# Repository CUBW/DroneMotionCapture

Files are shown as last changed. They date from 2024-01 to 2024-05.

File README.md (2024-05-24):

# Table of Contents

1. [System Overview](#1-system-overview)
2. [Basic Build and eCalc Statistics](#2-basic-build-and-ecalc-statistics)
3. [Physical Assembly](#3-physical-assembly)
   - [Flight Controller](#flight-controller)
   - [ESC](#electronic-speed-controller-esc)
   - [Raspberry Pi](#raspberry-pi)
4. [Firmware](#4-firmware)
   - [Flight Controller - ArduPilot/Kakute H7](#flight-controller---ardupilotkakute-h7)
   - [ESC](#electronic-speed-controller-esc-1)
   - [Raspberry Pi](#raspberry-pi-1)
5. [Raspberry Pi Antenna Setup](#5-raspberry-pi-antenna-setup)
   - [Pi ssh setup](#pi-ssh-setup)
   - [Pi UART setup](#pi-uart-setup)
   - [Pi Connection Example](#pi-connection-examples)
   - [Pi button setup](#pi-button-setup)
6. [Calibration/Tuning](#6-calibration/tuning)
   - []

## 1. System Overview
This system was created to create a foundation for more advanced Computer Science and Mechanical Engineering projects.
Goals for this project were:

Presise Control - We have a very small indoor flight space so presicsion/safety was important

Controlled Environment - We wanted the system be simple, but also very accurate, in order for users to be confident there is very little noise or inconsitancey in the system.

Computer Based Control - Lastly wanted control of system to be encapsulated in easy to use code library, allowing begginner proggrammers to use the system without low level knowlegde of communication or flight control. 

Ultimately, with these contraints in mind, we decided to create a Motion Capture Drone system. 
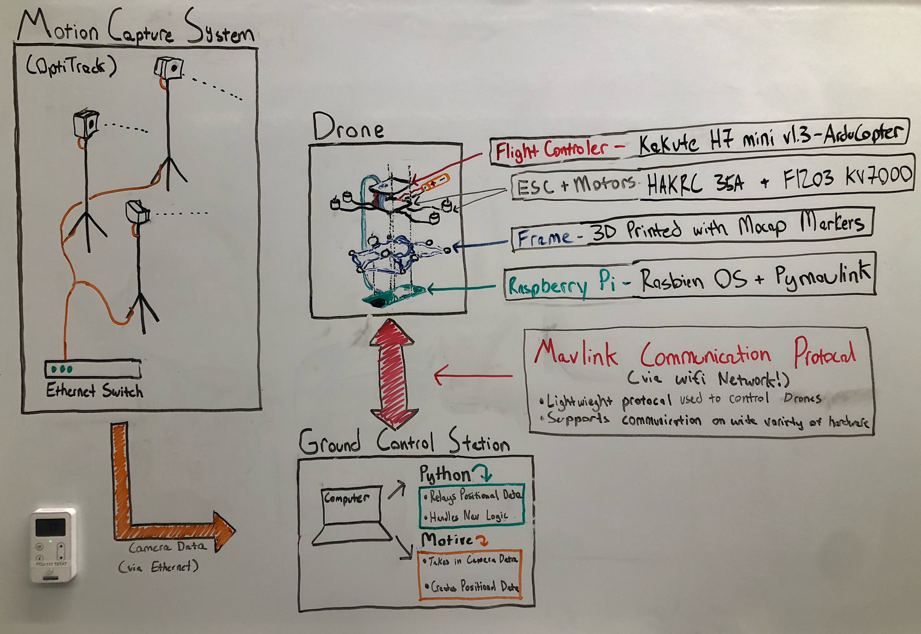
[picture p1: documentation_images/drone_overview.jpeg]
My Image


This system is comprised of three main components:

Drone: Custom built, running ArduCopter firmware, with Raspberry Pi (Using Pymavlink library)

Ground Control Computer: Running Python (Using Pymavlink library) + Motive (Optitrack Software)

Motion Capture System: 6 Cameras connected to ethernet switch (Connected to Ground Control Computer)

This system leverages the existing functionality of ArduCopter Firmware, and Mavlink Communication Protocal. Meaning this system can be immediately be used with ArduCopter UAV's or could be easily adapted to work with any UAV that utilized Mavlink Communication. 

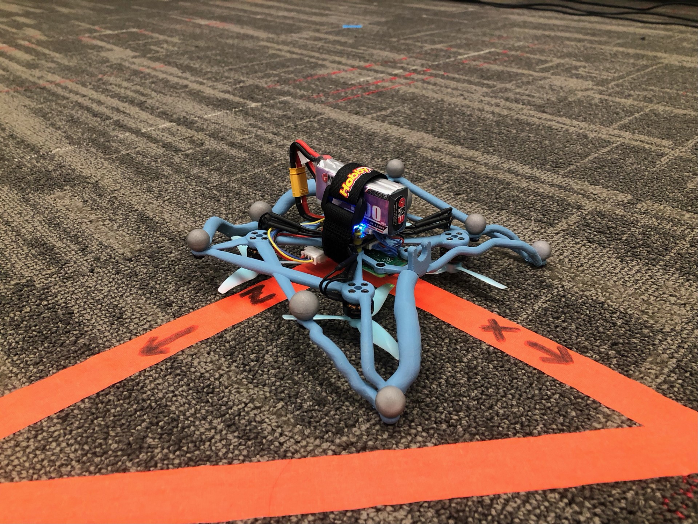
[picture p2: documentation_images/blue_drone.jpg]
My Image

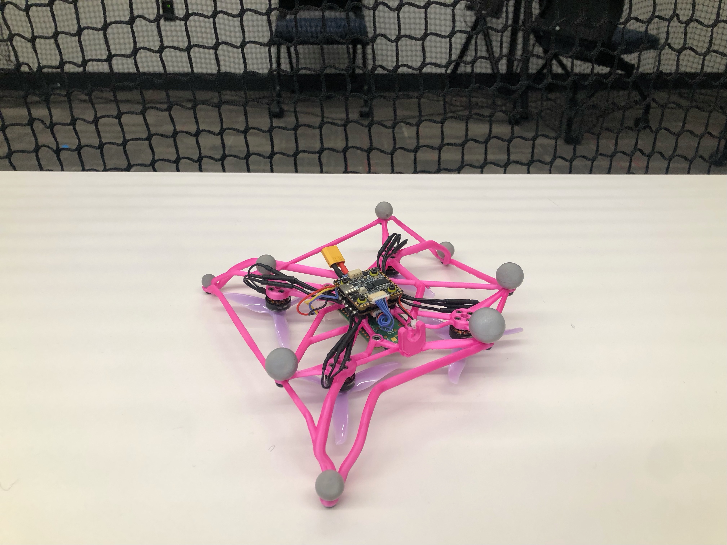
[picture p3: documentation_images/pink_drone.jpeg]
My Image


## 2. Basic Build and eCalc Statistics
First we need to build our drones! To confirm the performance of our proposed custom drone build, we use Ecalc Software. Ecalc takes in information about your custom drone, and predicts metrics such as Thrust:Weight and flight time

Basic Drone parts include, Frame, ESC, Motors, Props, and Batteries. Ecalc will also take into account the power draw of any drone components like Flight controller, FPV camera, and antenna. 
To begin we will make an Excel file with all of proposed parts, with summed weights, and power draws (not including motors)...

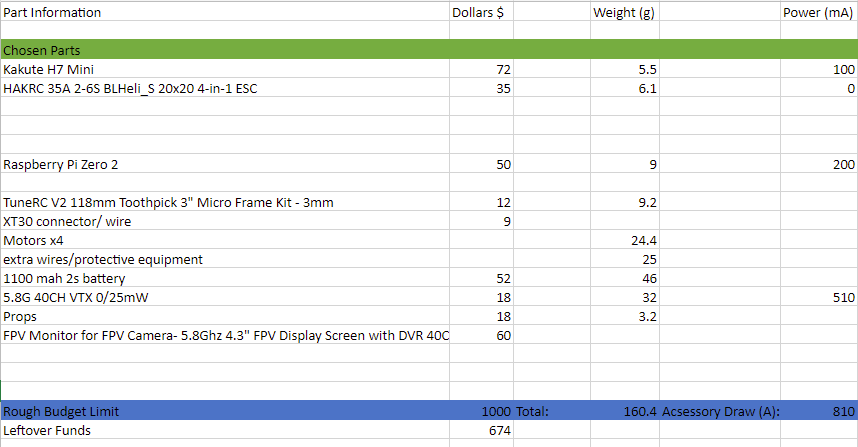
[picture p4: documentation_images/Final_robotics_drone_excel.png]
My Image


Note the totaled weights and power draw. Power draw does NOT include motors. 

Next step is to input this information into Ecalc ... 

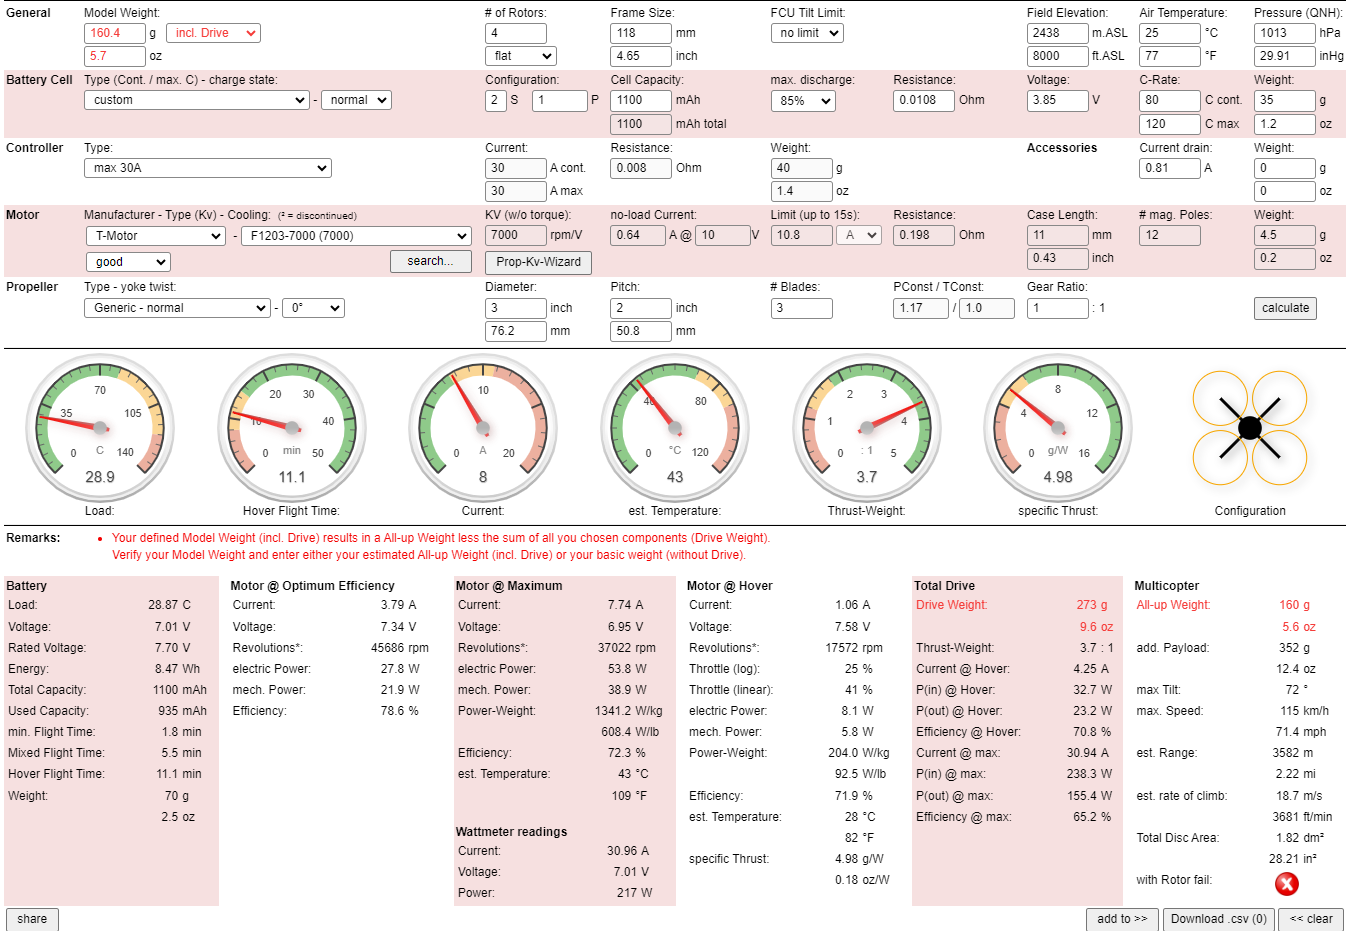
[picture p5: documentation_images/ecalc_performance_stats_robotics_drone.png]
My Image


Note we are using "Including Drive" as our weight option. This is because we have chosen all parts and know the actual weight. The other options beside "include drive" will asume your total weight doesn't include particular components and try to add those weights for you. In this case we can ignore the warning related to total weight, because the estimated weight that ecalc thinks this build should weigh is more than our actual parts. But since we went to the trouble of finding the actual total weight of our drone, we can ignore this. 

Take aways:

In order for our drone to be safely fly, Load, Current, Est. Temp, and Thrust-weight all have to be in the green. If these metrics are in yellow and red, drone my not be able to fly, or prone to damage itself. 

Flight time and Specific Thrust can be in Yellow or Red. Since we are going for an indoor drone with reasonably long flight time, our specific thrust is in the yellow. This is okay because specific thrust relates how effienctly our drone is turning wattage into thrust, and does not relate ablitly to drone to fly or possibly overheat. 

With this ecalc calculation we can confirm our drone will operate correctly with this combination of parts. 

## 3. Physical Assembly
### Flight Controller

For our flight controller we are using  Kakute h7 mini 1.3s. Compatible with Ardupilot Firmware. 

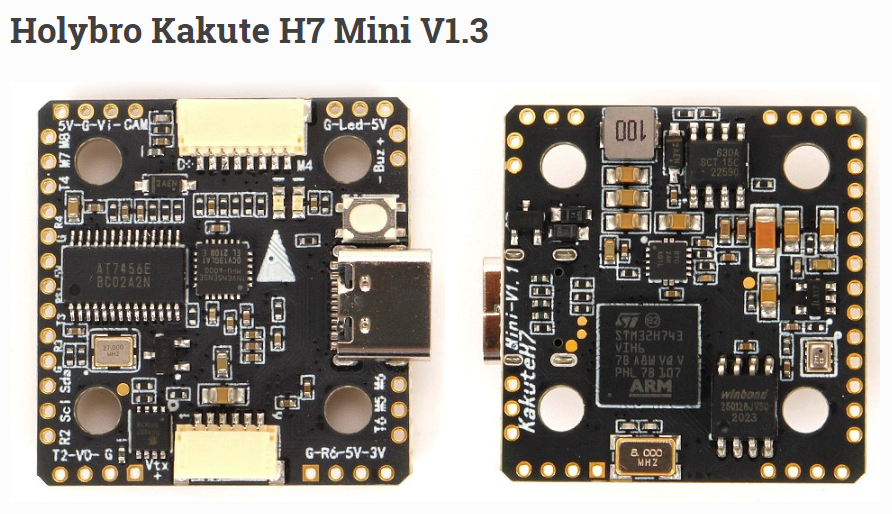
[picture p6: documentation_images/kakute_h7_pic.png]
My Image


For wiring with PI, we are using Pi only as antenna, so we much make four connections, 5v, Ground, Tx (transmit pin), and Rx (recieve pin). 

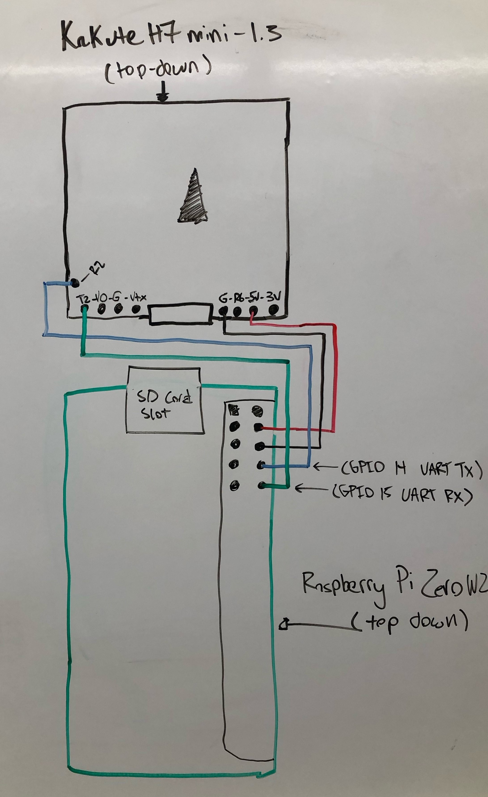
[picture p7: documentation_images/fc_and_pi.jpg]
My Image


For Wiring FPV Camera, our model has it's own antenna, so we only need 5v and GND

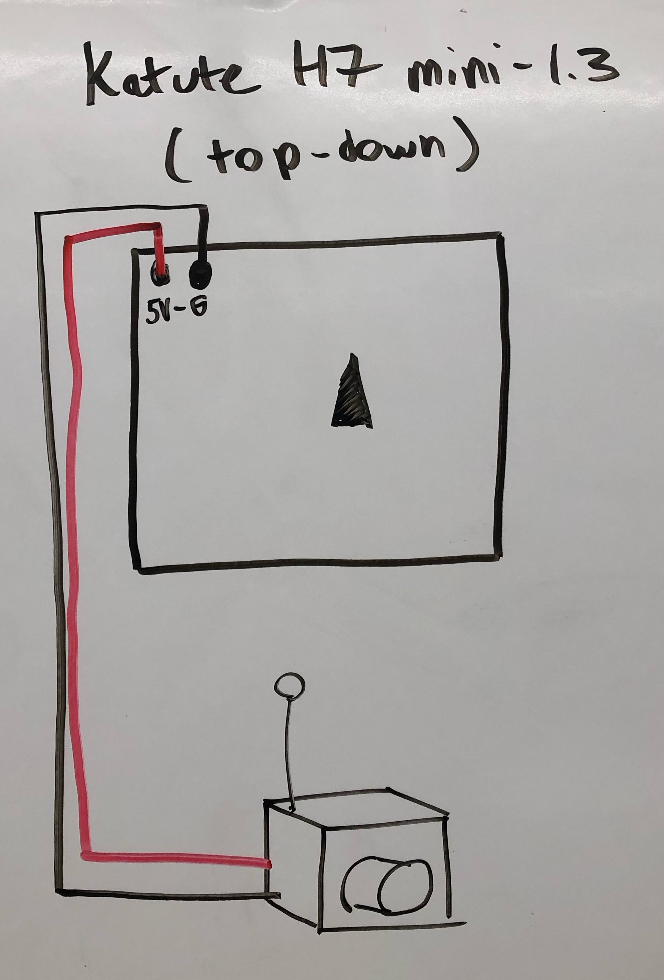
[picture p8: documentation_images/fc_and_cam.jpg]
My Image


### Raspberry Pi
Additionally, we added a button to the raspberry pi in order to properly turn off pi (Pi must be turned off before battery is unplugged, otherwise pi does not shut down correctly). 

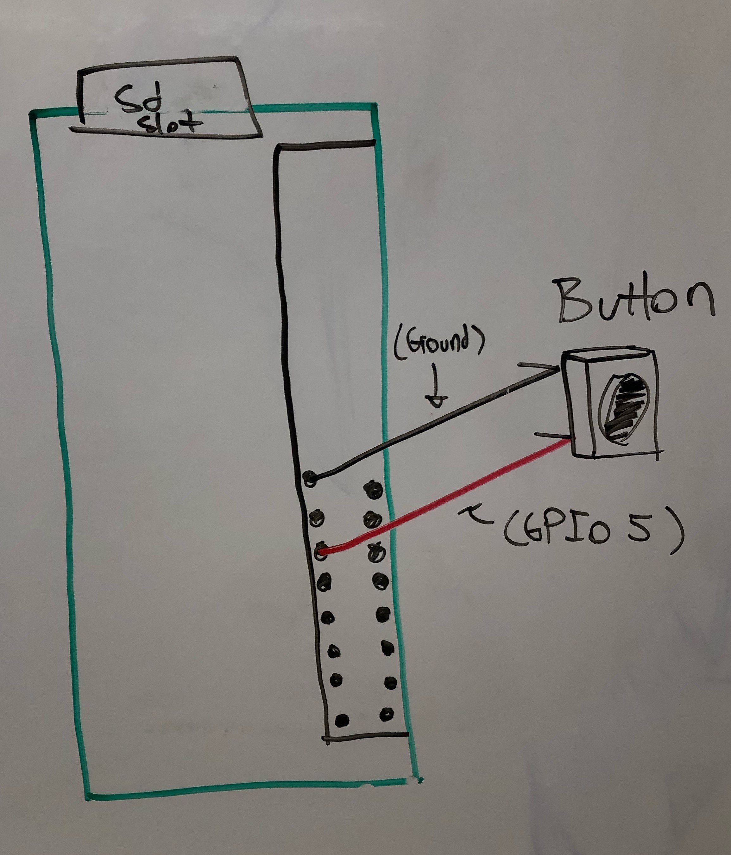
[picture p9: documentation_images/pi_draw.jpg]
My Image


### Electronic Speed Controller (ESC)
Flight controller comes with 6 pin JST connector, but our ESC has a different pin mapping, so the connector has been repinned as such:

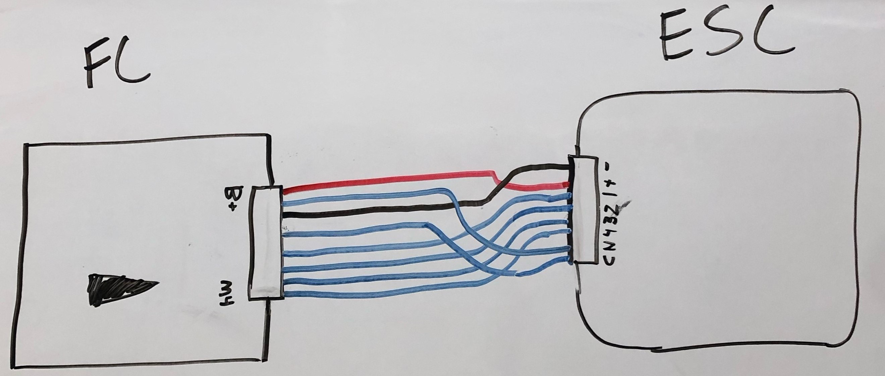
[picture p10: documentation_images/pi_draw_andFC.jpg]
My Image


ESC motor connections in general do not matter, motor will be able to move no matter how the three pins are connected to ESC. The only difference it makes is the direction the motor spins, which you are able to switch in ESC firmware if desired. However for ease of use, we decided to use pin connectors between motor and esc for easy direction swapping...

In addition to motors, a XT30 connector is soldered onto power connections of ESC this connects direclty to 1100mah 2s High Voltage Lipo Battery. 

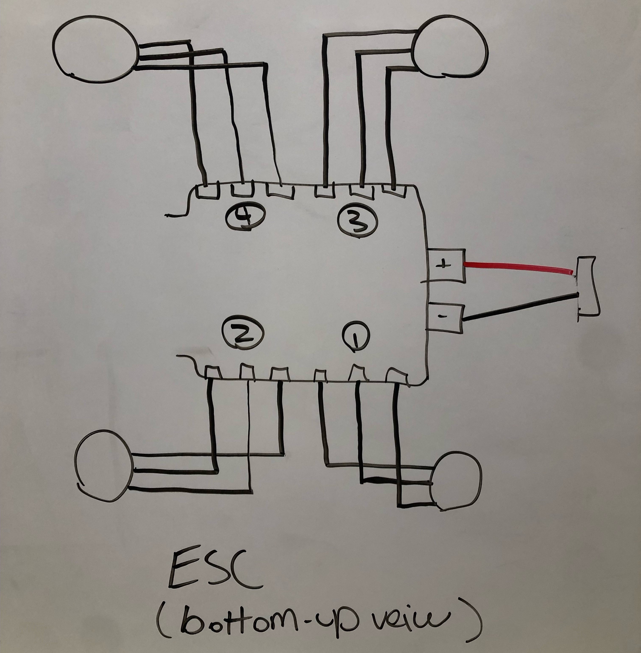
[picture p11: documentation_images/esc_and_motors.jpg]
My Image


## 4. Firmware
### Flight Controller - ArduPilot/Kakute H7
For our flight controller, we decided to use ArduCopter firmware. Exact version is included in Firmware folder. 
Or you can download latest version here: https://firmware.ardupilot.org/Copter/
#### STM32Cube Programmer and ArduCopter ISO
Installation guide follows general ArduCopter installation available here: https://ardupilot.org/copter/docs/common-loading-firmware-onto-chibios-only-boards.html

In Short the steps are: 

1. Download arducopter_with_bl.hex (from repo, or latest from: https://firmware.ardupilot.org/Copter/), we want "with_bl" because your esc is using running BLHeli_s...

2. Download and Install STM32CUBEProgrammer software: https://www.st.com/en/development-tools/stm32cubeprog.html

3. While holding down Kakute H7 mini's DFU button, connect to PC via USB

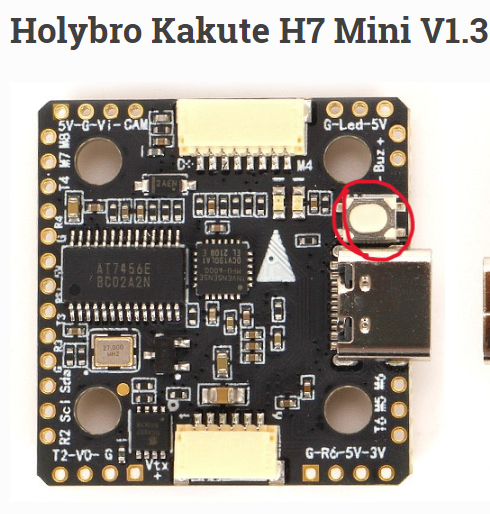
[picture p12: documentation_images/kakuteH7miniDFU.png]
My Image


4. "USB Configuration" hit the refresh button, the port should change from "No DFU detected" to "USB#" # being any number. Hit connect.

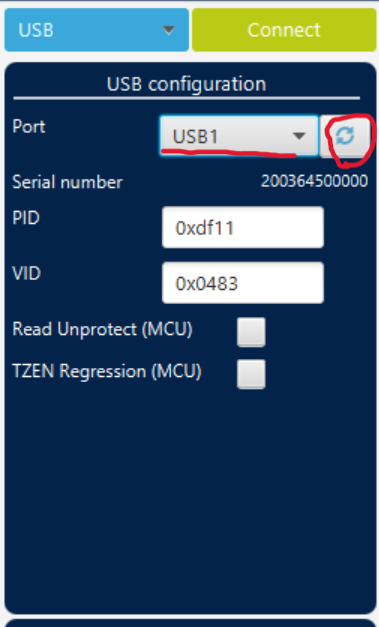
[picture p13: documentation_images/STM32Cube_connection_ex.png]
My Image


Then device information should display at bottom of USB configuration window.

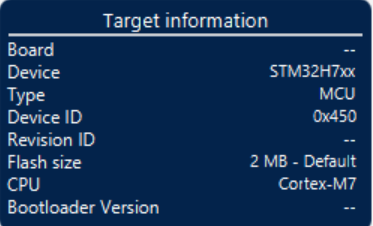
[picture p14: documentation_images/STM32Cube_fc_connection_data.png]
My Image


5. Now click the "open file" tab, and select the previously downloaded "arducopter_with_bl.hex"

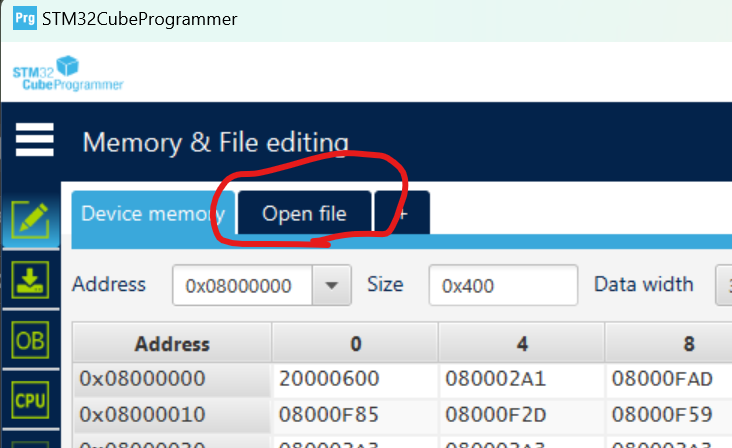
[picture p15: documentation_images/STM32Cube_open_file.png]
My Image


6. Lastly, hit download...

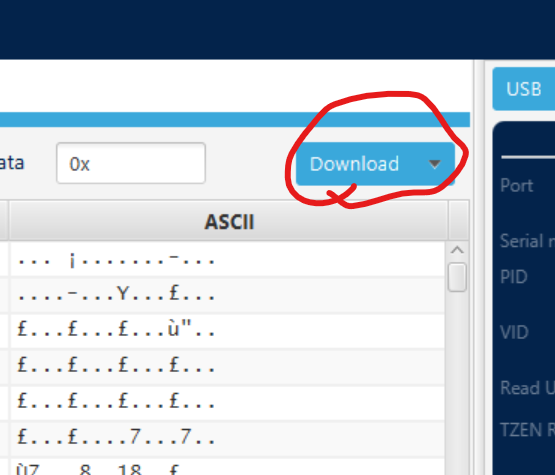
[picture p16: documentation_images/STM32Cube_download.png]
My Image


After this arducopter will install on flight controller and you can disconnect when you are done...

### Electronic Speed Controller (ESC)
Our esc comes with blheli_s, meaning we will use BLHeliSuite to configure esc settings NOT BLheliSuite32. In our setup the only purpose of using BLHeliSuite is to reverse the direction of motors, without rewiring them. You may not need to use this configuration software you don't need to swap directions without rewiring...

#### BLHeliSuite
1. Download and Launch BLHeliSuite, available here: https://www.mediafire.com/folder/dx6kfaasyo24l/BLHeliSuite

2. Power Flight controller and Esc via battery (FC and ESC are connected via the modified 8-pin JST connector referenced in hardware setup for FC). 

3. Once stack is powered by battery, plug flight controller into computer via USB.

4. In BLHeliSuite, click "Select ATMEL/SILABS Interface" drop down, and select "SILABS BLHeli Bootloader (cleanflight)" or the yellow "E". 

My Image

5. Now, in com window, select COM port that FC is currenlty connected under, Hit "connect", then hit "read setup"

My Image

Now you should be connected to ESC settings, and have the ability to modify ESC settings per motor. You can modify a single motor or muiltiple at same time by selecting motor numbers:

My Image

Then you can reversed motor direction for selected motors:

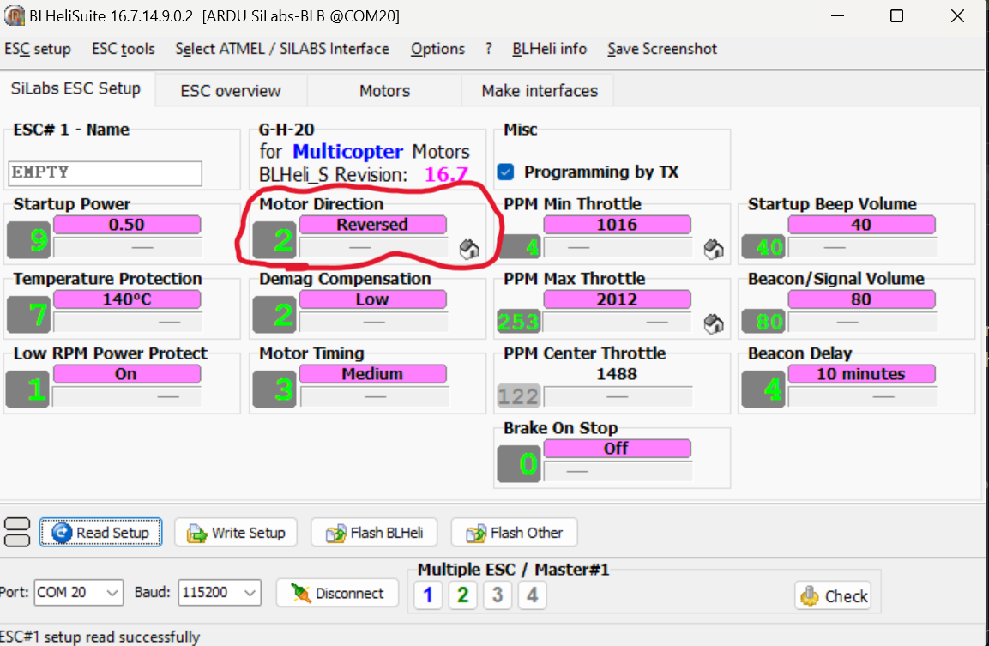
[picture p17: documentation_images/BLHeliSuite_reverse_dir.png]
My Image


### Raspberry Pi
We are using Raspberry Pi Zero 2 W, so we need to flash a Pi OS on an SD card. You can follow official documentation here: https://www.raspberrypi.com/documentation/computers/getting-started.html

Or follow the simplified steps below. 
#### Raspbian Image Flasher

1. Download and Install Rasbien Pi Imager: https://www.raspberrypi.com/software/
2. Start application, and plug in SD Card that Pi OS will be flashed on.
3. Click "Choose Device"

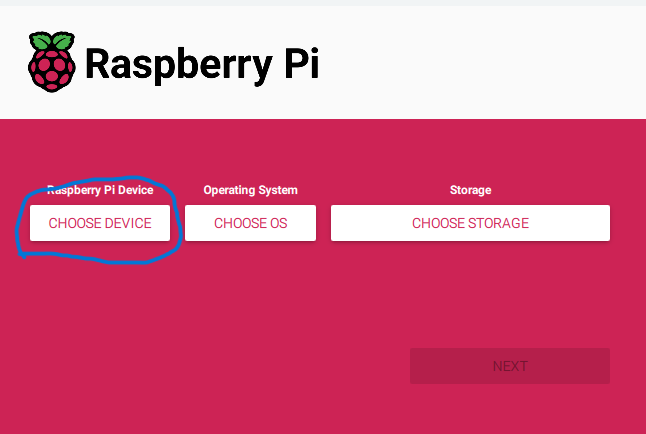
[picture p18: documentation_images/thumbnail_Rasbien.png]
My Image


4. Choose the Pi we are using, in this case Rasberry Pi Zero 2 W

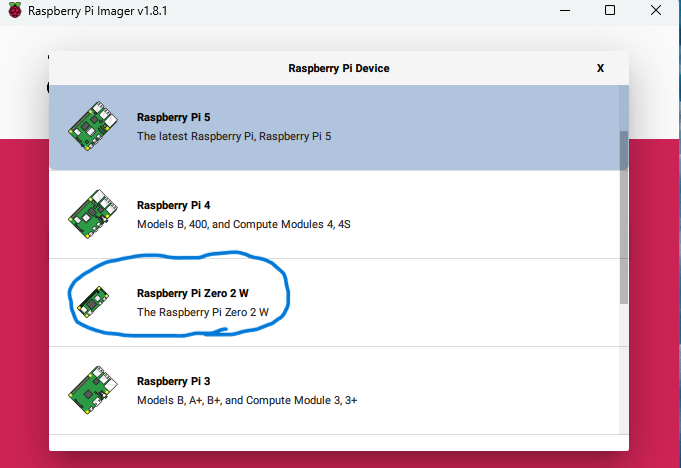
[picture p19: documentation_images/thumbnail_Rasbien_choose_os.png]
My Image

   
5. For the OS, since we have now need for Desktop GUI, we are opting to use "PI OS Lite" (no desktop env). To do this hit "Choose OS"

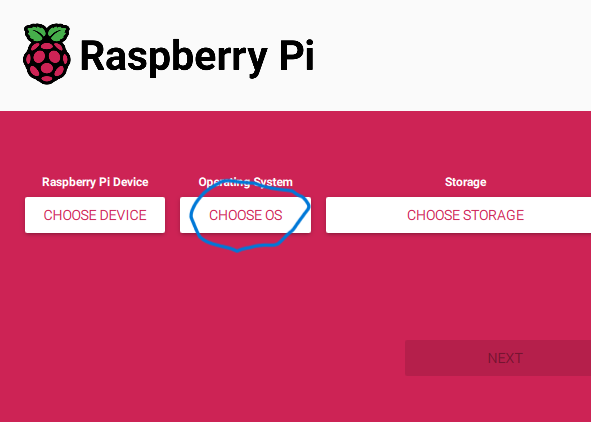
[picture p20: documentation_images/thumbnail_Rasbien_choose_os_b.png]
My Image


6. Select "Other" options

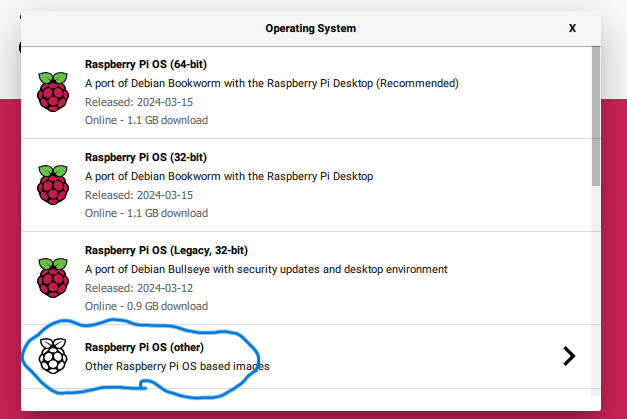
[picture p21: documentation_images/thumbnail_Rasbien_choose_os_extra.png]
My Image


7. Select "PI OS Lite (64 bit) 

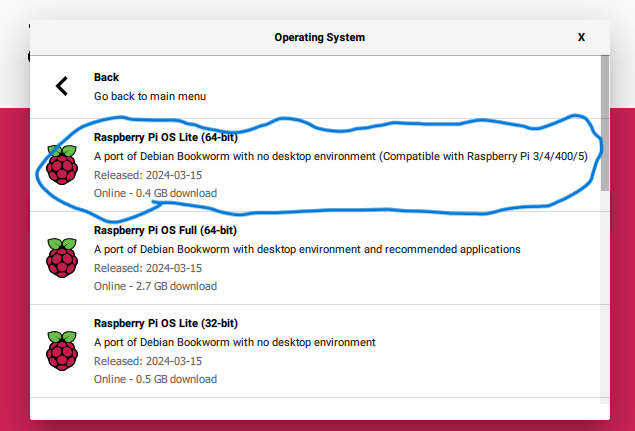
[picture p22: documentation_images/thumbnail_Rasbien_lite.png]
My Image


8. Now we must edit advanced settings, so Pi will automatically connect to a wifi network of our choosing. This is needed because we will be directly SSH into Pi. Select "Next" then seleect "edit settings". OR just click CTR + SHIFT + X on windows and linux. 

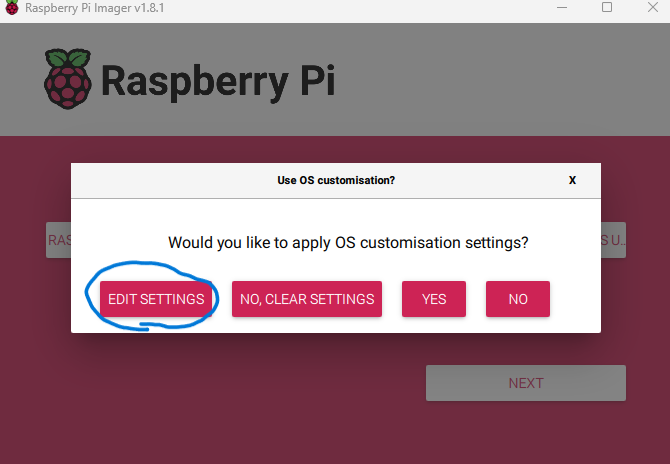
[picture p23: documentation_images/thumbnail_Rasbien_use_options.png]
My Image


9. Fill in all General settings. Hostname, Usernane, and Password will define how pi appears on local network and how to log into it (You will want to remember the username and password you set in "Set Username and Password" section). Configuration of wireless LAN is where you should put your network information (In our case the name and password to our wireless network). 

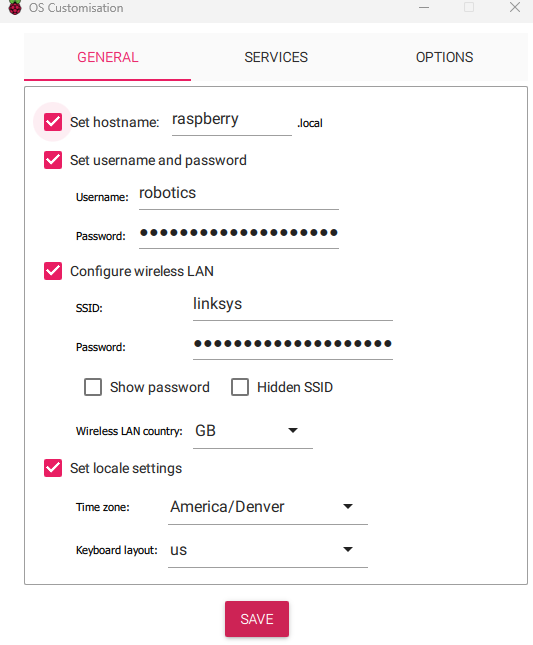
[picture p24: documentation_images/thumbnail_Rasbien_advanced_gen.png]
My Image


10. Next in the "Services" tab, make sure that SSH is enabled.

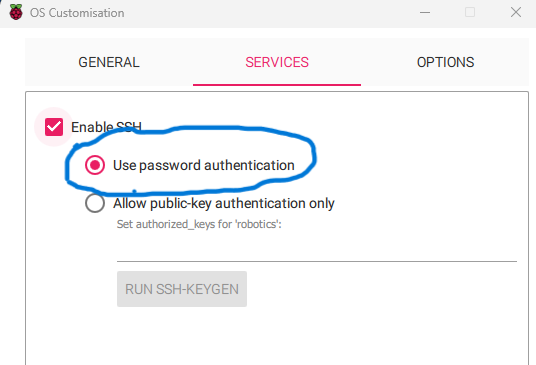
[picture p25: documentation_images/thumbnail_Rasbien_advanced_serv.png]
My Image


11. Lastly save all edited settings, (You don't need to change antything in "Options" Tab). Then confirm flashing of SD Card, then Wait for Rasbien to flash OS. SD Card should be good to plug into Pi once done!

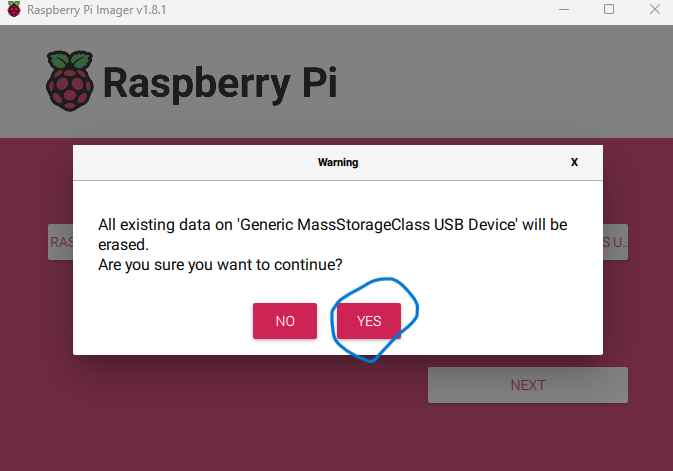
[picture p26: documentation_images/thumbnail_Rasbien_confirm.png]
My Image


## 5. Raspberry Pi Antenna Setup
The setup of Mavlink communication (Drone control) from ground computer through raspberry pi to flight controller follows the basic steps laid out in this guide: https://ardupilot.org/dev/docs/raspberry-pi-via-mavlink.html
Simplified steps for our use case are below...
### Flight Controller Params
First we must change some parameters on our Ardupilot Firmware, if you haven't arealdy installed the ardupilot firmware refer to Flight Controller in "Firmware" Section of documentation. 

We will be ajusting settings using Mission Planner ground control software built for ardupilot, this guide assumes basic knowlege of mission planner, and how to change paremeters. 

If you haven't used mission planner before it's strongly recommned to skim through the documentation, here are some useful links: 

Overview: https://ardupilot.org/dev/docs/raspberry-pi-via-mavlink.html

Installation steps: https://ardupilot.org/planner/docs/mission-planner-installation.html

Basics of Connecting: https://ardupilot.org/planner/docs/common-connect-mission-planner-autopilot.html

1. Connect FC directly to PC via USB C, then connect to FC with Mission Planner.

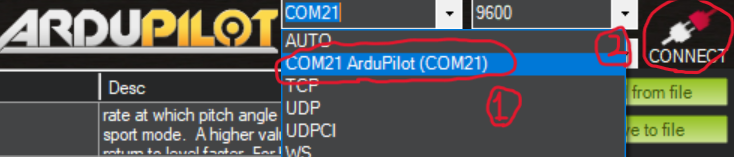
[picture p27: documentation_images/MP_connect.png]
My Image


2. Select "Config" Tab, then "Full Parameter List"

My Image
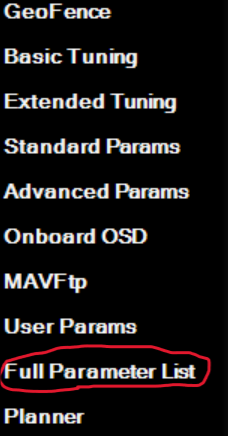
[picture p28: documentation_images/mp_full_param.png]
My Image


3. Change Serial2_protocal to 2 or mavlink 2. "Serial2" in our case are the RX and TX pins on our Kakute H7 mini Flight controller, we are telling the firmware to expect "Mavlink 2" communication protocal on those pins. 

My Image

4. Set Serial2_baud to 57600 (Note offical documentation recommends 921600, in our case we got the system working useing 57600)

My Image

5. Save Params and disconnect.

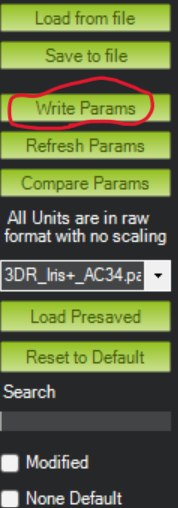
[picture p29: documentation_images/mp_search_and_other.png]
My Image
My Image

Flight contoller is ready to recieve and trasnmit mavlink messages on RX and TX pins that Pi is connectd to.

### Pi ssh setup
To configure Raspberry Pi we opted to SSH into Pi's command line over network. Since during the Pi's OS flasing, we uploaded the settings for Pi to connect automatically to our wifi network. We simply need to find the assigned IP address our local network has given our PI.

1. Power PI (with micro USB). Then, in our local network settings, Locate your routers "Dynamic Host Configuration Protocal Client Table" or "DHCP Cliets List" (This step may vary depending on router and firewall settings on wifi network...) In our case the IP address asigned to our drone is XXX.XXX.X.101, (Note I've put X placeholder in for security, the IP address will be all numbers). Also keep note of our Ground Control Computer in this case "Jayden's Laptop" with IP of XXX.XXX.X.106. 

My Image

2. Open Powershell or equivilant. Type "ssh robotics@XXX.XXX.X.XXX" XXX.XXX.X.XXX being the IP of the Pi we observed earlier. 

My Image

3. If connecting to Pi for first time (Or Ip has been reset for any reason), type "yes" for saving device.

My Image

4. You will then be prompted to type in a password. 
*NOTE: the username (in this case robotics) and password for PI are set when Flashing OS onto SD card, you should have them written down or saved somewhere. Refer to Section "Firmware" subsection "Rasberry PI" step #8 if you are confused...

My Image

If you've done everything correctly you should be SSH'd into PI, and able operate PI via command line interface

My Image

### Pi UART Setup

1. Now that you are ssh'd into pi, we need to open up UART pin to allow for mavlink communication to take place. In rasberry pi cmd line, type "sudo raspi-config"

2. You should open the raspberry pi's configuration menu, from here select "Interfacing Options"

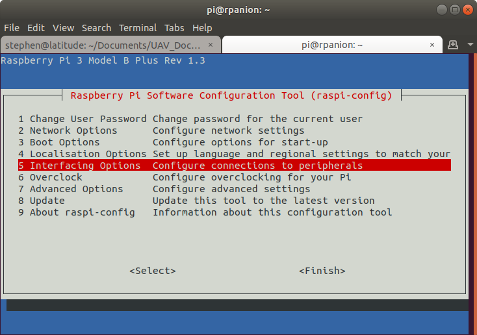
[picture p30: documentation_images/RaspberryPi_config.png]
My Image


3.. Now select "P6 Serial"

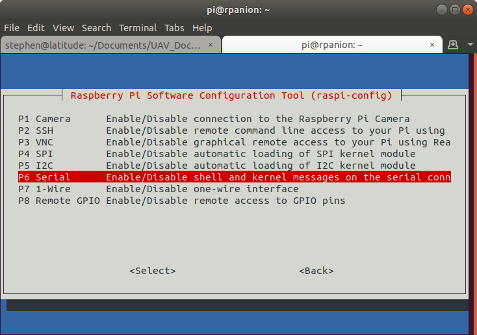
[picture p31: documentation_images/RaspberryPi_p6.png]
My Image


4. When prompted, select no to “Would you like a login shell to be accessible over serial?”.

5. When prompted, select yes to “Would you like the serial port hardware to be enabled?”.

6. Reboot the Raspberry Pi when you are done.

The Raspberry Pi’s serial port will now be usable on /dev/serial0.

### Pi MAVProxy Relay
Now we need to install mavproxy, both on our Pi and our Computer...
the official documentation is here: https://ardupilot.org/mavproxy/docs/getting_started/download_and_installation.html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
Simplified steps are:

1. SSH into Pi
2. Type use this code to install mavproxy (Install all dependencies! It may take 5-10 minutes)
```
sudo apt-get install python3-dev python3-opencv python3-wxgtk4.0 python3-pip python3-matplotlib python3-lxml python3-pygame
pip3 install PyYAML mavproxy --user
echo 'export PATH="$PATH:$HOME/.local/bin"' >> ~/.bashrc
```
For Windows MavProxy install use this installer (visit official documentation if this link is deptricated): https://firmware.ardupilot.org/Tools/MAVProxy/

### Pi Connection Examples
Now that Mavproxy has been installed, we are ready to use Rasberry Pi as "antenna" to control/calibrate our drone!

Example 1, Cmd line control directly from PI SSH Terminal
In this example we will ssh into pi and run MavProxy to connect it to flight controller. And control our drone by typing commands directly into Pi terminal over network

1. Power drone via charged battery (we don't need any wired connections to FC or Pi!)
2. Pi should power on automatically (if everything is wired correctly), SSH into pi
3. Run this code
```
 mavproxy.py --master=/dev/serial0 --baudrate 57600
```

It's important to note with in this example, Mavproxy is only being used as communication between the Pi and FC on the drone. We are using network (ssh) to type commands direclty to PI's terminal (running mavproxy). Ultimately, we want to establish mavlink communication across the network as well, to all allow other programs that use the Mavproxy communication protocal to talk directly to drone over network. see example 2. 

Example 2, Using Mavproxy as "relay" 
In this example we will now run mavproxy, and specify a local IP address for to relay it's mavlink connection to...

1. Access the IP address of your PI and Computer you desire to control drone from. In our case the unique identifiers of our IP addresses are Pi = .101 Computer = .106

My Image

2. SSH into PI, and run this command

Note the master is the same as the first example "/dev/serial0" this is the RX and TX uart connection to FC, the new startup argument out is the destination IP address that you with to relay our communication to. In our case the IP ending in .106

3. Open another PowerShell terminal on your computer, now simpley run mavproxy, no need to specify master or out

Congragulations we've acheived mavproxy communciation over wifi, if mavproxy connected correctly you should see the same cmd line interface for drone control that we saw when were direcly connectd over SSH. The only differnce now is that we have a Mavproxy is being used over network, not just between Pi and FC. 

What does this mean? 

Now that our pi is relaying our mavproxy connection to our computer's IP address. We can now connect with ardupilots "Mission Planner" Ground control software, but instead of using USB C wired connection. We can connect direcly to drone over wifi network. Which means we can now do all our conrol, calibration, and parameter changing wirelessly over the wifi network!

Example 3, connecting to drone with mission planner over network 

1. SSH into pi
2. Run Mavproxy code with XXX.XXX.X.XXX being the IP of your computer
3. Open Mission Planner, and in connection tab select "UDP", Baudrate of "57600" and port number of 14550

Now we are connected wirelessly with Mission planner!

### Pi Button Setup

## Flight Controller Configuration
### Motor, Frame, Propeller, and Battery
### Failsafes and Warnings
### Calibration

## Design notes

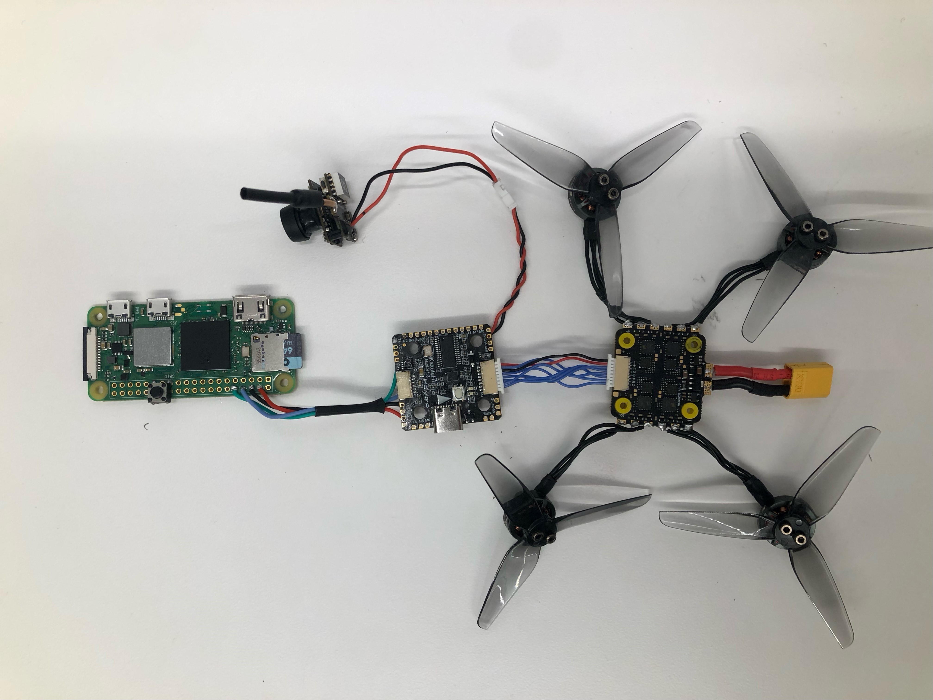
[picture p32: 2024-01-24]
documentation_images/whole_drone_pic.jpg

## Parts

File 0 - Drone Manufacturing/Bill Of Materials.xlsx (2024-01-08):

Part Information | Dollars $ |  | Weight (g) |  | Power (mA) | Shopping URL's | rough Delivery Time (days) | Documentation
Chosen Parts
Kakute H7 Mini | 72 |  | 5.5 |  | 100 | https://holybro.com/products/kakute-h7-mini
HAKRC 35A 2-6S BLHeli_S 20x20 4-in-1 ESC | 35 |  | 6.1 |  | 0 | https://www.getfpv.com/hakrc-35a-2-6s-blheli-s-20x20-4-in-1-esc.html
Raspberry Pi Zero 2 | 50 |  | 9 |  | 200 | https://www.sparkfun.com/products/18713?src=raspberrypi
TuneRC V2 118mm Toothpick 3" Micro Frame Kit - 3mm | 12 |  | 9.2 |  |  | https://www.racedayquads.com/products/tunerc-v2-118mm-3-toothpick-frame-kit-3mm?keyword=frame%203%22
XT30 connector/ wire | 9 |  |  |  |  | https://www.amazon.com/Hobbypark-Connectors-Silicone-Battery-Airplanes/dp/B08J7WPMD9
Motors x4 |  |  | 24.4
extra wires/protective equipment |  |  | 25
1100 mah 2s battery | 52 |  | 46 |  |  | https://www.amazon.com/GAONENG-Battery-1100mAh-Range-Connector/dp/B094NBH89Y
5.8G 40CH VTX 0/25mW | 18 |  | 32 |  | 510 | 5.8 (https://www.amazon.com/AKK-Switchable-600TVL-Camera-Inductrix/dp/B06Y5D8SPZ)
Props | 18 |  | 3.2
FPV Monitor for FPV Camera- 5.8Ghz 4.3" FPV Display Screen with DVR 40CH | 60 |  |  |  |  | https://www.amazon.com/Monitor-Camera-Display-Receiver-800x480/dp/B0BRQB1L2R
Rough Budget Limit | 1000 | Total: | 160.4 | Acsessory Draw (A): | 810
Leftover Funds | 674

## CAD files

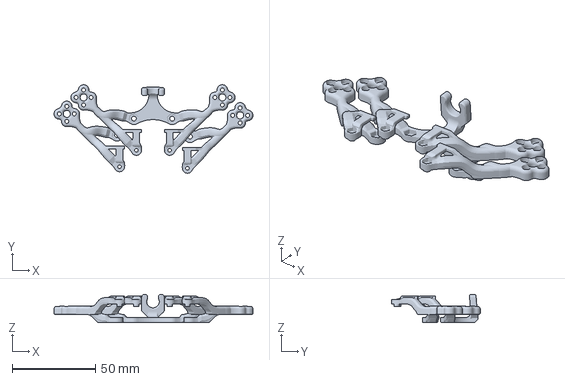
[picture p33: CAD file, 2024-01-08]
0 - Drone Manufacturing/Drone Frame.3mf
119.7 x 53.3 x 17.1 mm

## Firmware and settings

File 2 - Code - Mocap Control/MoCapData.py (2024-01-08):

#Copyright © 2021 Naturalpoint
#
#Licensed under the Apache License, Version 2.0 (the "License")
#you may not use this file except in compliance with the License.
#You may obtain a copy of the License at
#
#http://www.apache.org/licenses/LICENSE-2.0
#
#Unless required by applicable law or agreed to in writing, software
#distributed under the License is distributed on an "AS IS" BASIS,
#WITHOUT WARRANTIES OR CONDITIONS OF ANY KIND, either express or implied.
#See the License for the specific language governing permissions and
#limitations under the License.


# OptiTrack NatNet direct depacketization sample for Python 3.x
#


# Uses the Python NatNetClient.py library to establish a connection (by creating a NatNetClient),
# and receive data via a NatNet connection and decode it using the NatNetClient library.

#Utility functions

import copy
import hashlib
import random

K_SKIP = [0,0,1]
K_FAIL = [0,1,0]
K_PASS = [1,0,0]

# get_tab_str
# generate a string that takes the nesting level into account
def get_tab_str(tab_str, level):
    out_tab_str=""
    loop_range = range(0,level)
    for _ in loop_range:
        out_tab_str+=tab_str
    return out_tab_str

def add_lists(totals, totals_tmp):
    totals[0]+=totals_tmp[0]
    totals[1]+=totals_tmp[1]
    totals[2]+=totals_tmp[2]
    return totals

def test_hash(test_name, test_hash_str, test_object):
    out_str = test_object.get_as_string()
    out_hash_str=hashlib.sha1(out_str.encode()).hexdigest()
    ret_value=True
    if test_hash_str == out_hash_str:
        print("[PASS]:%s"%test_name)
    else:
        print("[FAIL]:%s test_hash_str != out_hash_str"%test_name)
        print("test_hash_str=%s"%test_hash_str)
        print("out_hash_str=%s"%out_hash_str)
        print("out_str =\n%s"%out_str)
        ret_value=False
    return ret_value


def test_hash2(test_name, test_hash_str, test_object, run_test=True):
    ret_value = K_FAIL
    out_str = "FAIL"
    out_str2=""
    indent_string="       "
    if not run_test:
        ret_value = K_SKIP
        out_str = "SKIP"
    elif test_object == None:
        out_str = "FAIL"
        ret_value = K_FAIL
        out_str2 = "%sERROR: test_object was None"%indent_string
    else:

        if str(type(test_object)) != 'NoneType':
            obj_out_str = test_object.get_as_string()
            obj_out_hash_str=hashlib.sha1(obj_out_str.encode()).hexdigest()

        if test_hash_str == obj_out_hash_str:
            out_str = "PASS"
            ret_value = K_PASS
        else:
            out_str2+="%s%s test_hash_str != out_hash_str\n"%(indent_string,test_name)
            out_str2+="%stest_hash_str=%s\n"%(indent_string,test_hash_str)
            out_str2+="%sobj_out_hash_str=%s\n"%(indent_string,obj_out_hash_str)
            out_str2+="%sobj_out_str =\n%s"%(indent_string,obj_out_str)
            ret_value = K_FAIL
    print("[%s]:%s"%(out_str,test_name))

    if len(out_str2):
        print("%s"%out_str2)
    return ret_value


def get_as_string(input_str):
    type_input_str=str(type(input_str))
    if type_input_str == "<class 'str'>":
        return input_str
    elif type_input_str ==  "<class 'NoneType'>":
        return ""
    elif type_input_str == "<class 'bytes'>":
        return input_str.decode('utf-8')
    else:
        print("type_input_str = %s NOT HANDLED"%type_input_str)
        return input_str


#MoCap Frame Classes
class FramePrefixData:
    def __init__(self, frame_number):
        self.frame_number=frame_number

    def get_as_string(self,tab_str="  ", level = 0):
        out_tab_str = get_tab_str(tab_str, level)
        out_str = "%sFrame #: %3.1d\n"%(out_tab_str,self.frame_number)
        return out_str

class MarkerData:
    def __init__(self):
        self.model_name=""
        self.marker_pos_list=[]

    def set_model_name(self, model_name):
        self.model_name = model_name

    def add_pos(self, pos):
        self.marker_pos_list.append(copy.deepcopy(pos))
        return len(self.marker_pos_list)


    def get_num_points(self):
        return len(self.marker_pos_list)


    def get_as_string(self, tab_str="  ", level=0):
        out_tab_str = get_tab_str(tab_str, level)
        out_tab_str2 = get_tab_str(tab_str, level+1)
        out_str=""
        out_str+="%sMarkerData:\n"%out_tab_str
        if self.model_name != "":
            out_str+="%sModel Name : %s\n"%(out_tab_str, get_as_string(self.model_name))
        marker_count = len(self.marker_pos_list)
        out_str+="%sMarker Count :%3.1d\n"%(out_tab_str, marker_count)
        for i in range(marker_count):
            pos = self.marker_pos_list[i]
            out_str+="%sMarker %3.1d pos : [x=%3.2f,y=%3.2f,z=%3.2f]\n"%(out_tab_str2,i,pos[0], pos[1], pos[2])
        return out_str

class MarkerSetData:
    def __init__(self):
        self.marker_data_list=[] #List of Mocap data, the contents of which we will send to the drone
        self.unlabeled_markers=MarkerData()
        self.unlabeled_markers.set_model_name("")

    def add_marker_data(self, marker_data):
        self.marker_data_list.append(copy.deepcopy(marker_data))
        return len(self.marker_data_list)

    def add_unlabeled_marker(self, pos):
        self.unlabeled_markers.add_pos(pos)

    def get_marker_set_count(self):
        return len(self.marker_data_list)

    def get_unlabeled_marker_count(self):
        return self.unlabeled_markers.get_num_points()
    def get_as_string(self, tab_str="  ", level=0):
        out_tab_str  = get_tab_str(tab_str, level)


        out_str=""

        # Labeled markers count
        marker_data_count = len(self.marker_data_list)
        out_str+= "%sMarker Set Count:%3.1d\n"% (out_tab_str,marker_data_count)
        for marker_data in self.marker_data_list:
            out_str += marker_data.get_as_string(tab_str,level+1)

        # Unlabeled markers count (4 bytes)
        unlabeled_markers_count = self.unlabeled_markers.get_num_points()
        out_str += "%sUnlabeled Markers Count:%3.1d\n"%(out_tab_str, unlabeled_markers_count )
        out_str += self.unlabeled_markers.get_as_string(tab_str,level+1)
        return out_str

class LegacyMarkerData:
    def __init__(self):
        self.marker_pos_list=[]

    def add_pos(self, pos):
        self.marker_pos_list.append(copy.deepcopy(pos))
        return len(self.marker_pos_list)

    def get_marker_count(self):
        return len(self.marker_pos_list)

    def get_as_string(self, tab_str="  ", level=0):
        out_tab_str = get_tab_str(tab_str, level)
        out_tab_str2 = get_tab_str(tab_str, level+1)
        out_str=""
        marker_count = len(self.marker_pos_list)
        out_str+="%sLegacy Marker Count :%3.1d\n"%(out_tab_str, marker_count)
        for i in range(marker_count):
            pos = self.marker_pos_list[i]
            # The line below shows how the points lie in the array, this is what we will send to the drone for position, still working on altitude
            out_str+="%sMarker %3.1d pos : [x=%3.2f,y=%3.2f,z=%3.2f]\n"%(out_tab_str2,i,pos[0], pos[1], pos[2])
        return out_str

class RigidBodyMarker:
    def __init__(self):
        self.pos = [0.0,0.0,0.0]
        self.id_num = 0
        self.size = 0
        self.error = 0

    def get_as_string(self, tab_str="  ", level=0):
        out_tab_str = get_tab_str(tab_str, level)
        out_str = ""
        out_str+="RBMarker:\n"
        out_str += "%sPosition: [%3.2f %3.2f %3.2f]\n"%( out_tab_str, self.pos[0], self.pos[1], self.pos[2] )
        out_str += "%sID      : %3.1d\n"%(out_tab_str, self.id_num)
        out_str += "%sSize    : %3.1d\n"%(out_tab_str, self.size)
        return out_str


class RigidBody:
    def __init__(self, new_id, pos, rot):
        self.id_num = new_id
        self.pos=pos
        self.rot=rot
        self.rb_marker_list=[]
        self.tracking_valid = False
        self.error = 0.0

    def add_rigid_body_marker(self, rigid_body_marker):
        self.rb_marker_list.append(copy.deepcopy(rigid_body_marker))
        return len(self.rb_marker_list)


    def get_as_string(self, tab_str=0, level=0):
        out_tab_str = get_tab_str(tab_str, level)
        out_tab_str2 = get_tab_str(tab_str, level+1)

        out_str=""

        # header
        out_str += "%sID            : %3.1d\n"% (out_tab_str, self.id_num)
        # Position and orientation
        out_str += "%sPosition      : [%3.2f, %3.2f, %3.2f]\n"% (out_tab_str, self.pos[0], self.pos[1], self.pos[2] )
        out_str += "%sOrientation   : [%3.2f, %3.2f, %3.2f, %3.2f]\n"% (out_tab_str, self.rot[0], self.rot[1], self.rot[2], self.rot[3] )

        marker_count = len(self.rb_marker_list)
        marker_count_range = range( 0, marker_count )

        # Marker Data
        if marker_count > 0:
            out_str += "%sMarker Count: %3.1d\n"%(out_tab_str, marker_count )
            for i in marker_count_range:
                out_str += "%sMarker %3.1d\n"%(out_tab_str2, i)
                rbmarker = self.rb_marker_list[i]
                out_str += rbmarker.get_as_string(tab_str, level+2)

        out_str += "%sMarker Error  : %3.2f\n"% (out_tab_str, self.error)

        # Valid Tracking
        tf_string = 'False'
        if self.tracking_valid:
            tf_string = 'True'
        out_str += "%sTracking Valid: %s\n"%(out_tab_str, tf_string)

        return out_str


class RigidBodyData:
    def __init__(self):
        self.rigid_body_list=[]


    def add_rigid_body(self, rigid_body):
        self.rigid_body_list.append(copy.deepcopy(rigid_body))
        return len(self.rigid_body_list)


    def get_rigid_body_count(self):
        return len(self.rigid_body_list)


    def get_as_string(self, tab_str="  ", level=0):
        out_tab_str = get_tab_str(tab_str, level)
        out_str=""
        rigid_body_count=len(self.rigid_body_list)
        out_str += "%sRigid Body Count: %3.1d\n"%(out_tab_str, rigid_body_count)
        for rigid_body in self.rigid_body_list:
            out_str += rigid_body.get_as_string(tab_str, level+1)
        return out_str

class Skeleton:
    def __init__(self, new_id=0):
        self.id_num=new_id
        self.rigid_body_list=[]


    def add_rigid_body(self, rigid_body):
        self.rigid_body_list.append(copy.deepcopy(rigid_body))
        return len(self.rigid_body_list)


    def get_as_string(self, tab_str="  ", level=0):
        out_tab_str = get_tab_str(tab_str, level)
        out_tab_str2 = get_tab_str(tab_str, level+1)
        out_str=""
        out_str+="Skeleton:\n"
        out_str+="%sID: %3.1d\n"%(out_tab_str, self.id_num)
        rigid_body_count=len(self.rigid_body_list)
        out_str += "%sRigid Body Count: %3.1d\n"%(out_tab_str, rigid_body_count)
        for rb_num in range(rigid_body_count):
            out_str += "%sRigid Body %3.1d\n"%(out_tab_str2, rb_num)
            out_str += self.rigid_body_list[rb_num].get_as_string(tab_str, level+2)
        return out_str


class SkeletonData:
    def __init__(self):
        self.skeleton_list=[]


    def add_skeleton(self, new_skeleton):
        self.skeleton_list.append(copy.deepcopy(new_skeleton))


    def get_skeleton_count(self):
        return len(self.skeleton_list)


    def get_as_string(self, tab_str = "  ", level=0):
        out_tab_str = get_tab_str(tab_str, level)
        out_tab_str2 = get_tab_str(tab_str, level+1)

        out_str = ""
        skeleton_count = len(self.skeleton_list)
        out_str += "%sSkeleton Count: %3.1d\n"%(out_tab_str, skeleton_count)
        for skeleton_num in range(skeleton_count):
            out_str += "%sSkeleton %3.1d\n"%(out_tab_str2, skeleton_num)
            out_str += self.skeleton_list[skeleton_num].get_as_string(tab_str, level+2)
        return out_str

class AssetMarkerData:
    def __init__(self, marker_id, pos, marker_size=0.0, marker_params=0, residual=0.0):
        self.marker_id=marker_id
        self.pos=pos
        self.marker_size=marker_size
        self.marker_params=marker_params
        self.residual=residual

    def get_as_string(self, tab_str="  ", level=0):
        out_tab_str = get_tab_str(tab_str, level)
        out_tab_str2 = get_tab_str(tab_str, level+1)
        out_str=""
        out_str+="%sID       : %s\n"%(out_tab_str, get_as_string(self.marker_id))
        out_str+="%sPos      : %3.2f %3.2f %3.2f\n"%(out_tab_str, self.pos[0], self.pos[1], self.pos[2])
        out_str+="%sSize     : %3.2f\n"%(out_tab_str, self.marker_size)
        out_str+="%sParams   : %s\n"%(out_tab_str, self.marker_params)
        out_str+="%sResidual : %3.2f\n"%(out_tab_str, self.residual)

        return out_str

class AssetRigidBodyData:
    def __init__(self, new_id, pos, rot, mean_error=0.0, param=0):
        self.id_num=new_id
        self.pos = pos
        self.rot = rot
        self.mean_error = mean_error
        self.param = param

    def get_as_string(self, tab_str="  ", level=0):
        out_tab_str = get_tab_str(tab_str, level)
        out_str=""
        out_str += "%sID          : %s\n"%(out_tab_str, get_as_string(self.marker_id))
        out_str += "%sPosition    : %3.2f %3.2f %3.2f\n"%(out_tab_str, self.pos[0], self.pos[1], self.pos[2])
        out_str += "%sOrientation : %3.2f %3.2f %3.2f %3.2f\n"%(out_tab_str, self.rot[0], self.rot[1], self.rot[2], self.rot[3])
        out_str += "%sMean Error  : %3.2f\n"%(out_tab_str, self.mean_error)
        out_str += "%sParam       : %s\n"%(out_tab_str, self.param)

        return out_str

class AssetData:
    def __init__(self):
        self.asset_id=0
        self.asset_rigid_body_list=[]
        self.asset_marker_list=[]

    def set_id(self, new_id):
        self.asset_id=new_id

    def add_rigid_body(self, rigid_body):
        self.rigid_body_list.append(copy.deepcopy(rigid_body))
        return len(self.rigid_body_list)

    def add_marker(self, marker):
        self.marker_list.append(copy.deepcopy(marker))
        return len(self.marker_list)

    def get_rigid_body_count(self):
        return len(self.asset_rigid_body_list)

    def get_marker_count(self):
        return len(self.asset_marker_list)

    def get_as_string(self, tab_str = "  ", level = 0):
        out_tab_str = get_tab_str(tab_str, level)

        out_str = ""
        out_str+="%sAssetData:\n"%out_tab_str
        out_str += "%sID          :%s"%(out_tab_str,get_as_string(self.asset_id))
        rigid_body_count = len(self.rigid_body_list)
        out_str += "%srigid_body Count: %3.1d\n"%(out_tab_str, rigid_body_count)
        for i in range(rigid_body_count):
            out_str += self.rigid_body_list[i].get_as_string(tab_str, level+1, i)

        marker_count = len(self.marker_list)
        out_str += "%smarker Count: %3.1d\n"%(out_tab_str, marker_count)
        for i in range(marker_count):
            out_str += self.marker_list[i].get_as_string(tab_str, level+1, i)

        return out_str


class LabeledMarker:
    def __init__(self, new_id, pos, size=0.0, param = 0, residual=0.0):
        self.id_num=new_id
        self.pos = pos
        self.size = size
        self.param = param
        self.residual = residual
        if str(type(size)) == "<class 'tuple'>":
            self.size=size[0]

    def __decode_marker_id(self):
        model_id = self.id_num >> 16
        marker_id = self.id_num & 0x0000ffff
        return model_id, marker_id

    def __decode_param(self):
        occluded = ( self.param & 0x01 ) != 0
        point_cloud_solved = ( self.param & 0x02 ) != 0
        model_solved = ( self.param & 0x04 ) != 0
        return occluded,point_cloud_solved, model_solved

    def get_as_string(self, tab_str, level):
        out_tab_str = get_tab_str(tab_str, level)
        model_id, marker_id = self.__decode_marker_id()
        out_str = ""
        out_str+="%sLabeledMarker:\n"%out_tab_str
        out_str += "%sID                 : [MarkerID: %3.1d] [ModelID: %3.1d]\n"%(out_tab_str, marker_id,model_id)
        out_str += "%spos                : [%3.2f, %3.2f, %3.2f]\n"%(out_tab_str, self.pos[0],self.pos[1],self.pos[2])
        out_str += "%ssize               : [%3.2f]\n"%(out_tab_str, self.size)

        occluded, point_cloud_solved, model_solved = self.__decode_param()
        out_str += "%soccluded           : [%3.1d]\n"%(out_tab_str, occluded)
        out_str += "%spoint_cloud_solved : [%3.1d]\n"%(out_tab_str, point_cloud_solved)
        out_str += "%smodel_solved       : [%3.1d]\n"%(out_tab_str, model_solved)
        out_str += "%serr                : [%3.2f]\n"%(out_tab_str, self.residual)

        return out_str


class LabeledMarkerData:
    def __init__(self):
        self.labeled_marker_list=[]

    def add_labeled_marker(self, labeled_marker):
        self.labeled_marker_list.append(copy.deepcopy(labeled_marker))
        return len(self.labeled_marker_list)

    def get_labeled_marker_count(self):
        return len(self.labeled_marker_list)

    def get_as_string(self, tab_str = "  ", level = 0):
        out_tab_str = get_tab_str(tab_str, level)
        out_tab_str2 = get_tab_str(tab_str, level+1)
        out_str = ""

        labeled_marker_count = len(self.labeled_marker_list)
        out_str += "%sLabeled Marker Count:%3.1d\n"%(out_tab_str, labeled_marker_count )
        for i in range( 0, labeled_marker_count ):
            out_str += "%sLabeled Marker %3.1d\n"%(out_tab_str2,i)
            labeled_marker = self.labeled_marker_list[i]
            out_str += labeled_marker.get_as_string(tab_str, level+2)
        return out_str

class ForcePlateChannelData:
    def __init__(self):
        # list of floats
        self.frame_list=[]


    def add_frame_entry(self, frame_entry):
        self.frame_list.append(copy.deepcopy(frame_entry))
        return len(self.frame_list)


    def get_as_string(self, tab_str, level, channel_num = -1):
        fc_max = 4
        out_tab_str  = get_tab_str(tab_str, level)

        out_str = ""
        frame_count = len(self.frame_list)
        fc_show = min(frame_count, fc_max)
        out_str += "%s"%(out_tab_str)
        if channel_num >= 0 :
            out_str += "Channel %3.1d: "%channel_num
        out_str += "%3.1d Frames - Frame Data: "%(frame_count)
        for i in range(fc_show):
            out_str += "%3.2f "%(self.frame_list[i])
        if fc_show < frame_count :
            out_str += " - Showing %3.1d of %3.1d frames"%(fc_show, frame_count)
        out_str += "\n"
        return out_str

class ForcePlate:
    def __init__(self, new_id=0):
        self.id_num = new_id
        self.channel_data_list=[]

    def add_channel_data(self, channel_data):
        self.channel_data_list.append(copy.deepcopy(channel_data))
        return len(self.channel_data_list)

    def get_as_string(self, tab_str, level):
        out_tab_str = get_tab_str(tab_str, level)
        out_str = ""

        out_str += "%sID           : %3.1d"%(out_tab_str, self.id_num)
        num_channels = len(self.channel_data_list)
        out_str += "%sChannel Count: %3.1d\n"%(out_tab_str, num_channels)
        for i in range(num_channels):
            out_str += self.channel_data_list[i].get_as_string(tab_str, level+1,i)
        return out_str

class ForcePlateData:
    def __init__(self):
        self.force_plate_list=[]

    def add_force_plate(self, force_plate):
        self.force_plate_list.append(copy.deepcopy(force_plate))
        return len(self.force_plate_list)


    def get_force_plate_count(self):
        return len(self.force_plate_list)


    def get_as_string(self, tab_str="  ", level=0):
        out_tab_str = get_tab_str(tab_str, level)
        out_tab_str2 = get_tab_str(tab_str, level+1)
        out_str=""

        force_plate_count = len(self.force_plate_list)
        out_str += "%sForce Plate Count: %3.1d\n"%(out_tab_str, force_plate_count)
        for i in range(force_plate_count):
            out_str += "%sForce Plate %3.1d\n"%(out_tab_str2, i)
            out_str += self.force_plate_list[i].get_as_string(tab_str, level+2)

        return out_str

class DeviceChannelData:
    def __init__(self):
        # list of floats
        self.frame_list=[]


    def add_frame_entry(self, frame_entry):
        self.frame_list.append(copy.deepcopy(frame_entry))
        return len(self.frame_list)


    def get_as_string(self, tab_str, level, channel_num = -1):
        fc_max = 4
        out_tab_str  = get_tab_str(tab_str, level)

        out_str = ""
        frame_count = len(self.frame_list)
        fc_show = min(frame_count, fc_max)
        out_str += "%s"%(out_tab_str)
        if channel_num >= 0:
            out_str += "Channel %3.1d: "%channel_num
        out_str += "%3.1d Frames - Frame Data: "%(frame_count)
        for i in range(fc_show):
            out_str += "%3.2f "%(self.frame_list[i])
        if fc_show < frame_count:
            out_str += " - Showing %3.1d of %3.1d frames"%(fc_show, frame_count)
        out_str += "\n"
        return out_str


class Device:
    def __init__(self, new_id):
        self.id_num=new_id
        self.channel_data_list = []

    def add_channel_data(self, channel_data):
        self.channel_data_list.append(copy.deepcopy(channel_data))
        return len(self.channel_data_list)

    def get_as_string(self, tab_str, level, device_num):
        out_tab_str = get_tab_str(tab_str, level)

        out_str = ""

        num_channels = len(self.channel_data_list)
        out_str+= "%sDevice %3.1d      ID: %3.1d Num Channels: %3.1d\n"% (out_tab_str, device_num, self.id_num, num_channels )
        for i in range(num_channels):
            out_str += self.channel_data_list[i].get_as_string(tab_str, level+1, i)

        return out_str
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

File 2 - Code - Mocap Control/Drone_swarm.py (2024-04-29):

import sys
import time
from Custom_Drone_Commands import *
from Custom_Mocap_Commands import *   


###### MAIN ######
init_time = time.time()

num_of_drones = 2

# Mocap connection:
streaming_client = mocap_connect()

is_running = streaming_client.run()


# Drone connection
swarm_ports = [14550, 14551, 14552] 
swarm_connections= []
swarm_mocap_streaming_threads = []

for port in swarm_ports:
    connection = drone_connect(port)
    swarm_connections.append(connection)

time.sleep(3)
# Mocap Streaming Thread, will run until you terminate THIS's files terminal.

swarm_rigid_body_id_list = [6,9,8]

stream_id = 1
for id, connection in zip(swarm_rigid_body_id_list, swarm_connections):
    stream_id_string = "stream" + str(stream_id)
    threaded_mocap_drone_stream = threaded_mocap_streaming(stream_id_string, stream_id, connection, streaming_client, init_time, id)
    swarm_mocap_streaming_threads.append(threaded_mocap_drone_stream)

accuracy = .10

for drone_mocap_thread_stream in swarm_mocap_streaming_threads:
    drone_mocap_thread_stream.start()

time.sleep(2)
for drone_connection in swarm_connections:
    set_drone_gps_global_origin(drone_connection)
time.sleep(3)

take_off_height = .5
drone1_takeoff_thread = TakeoffThread(swarm_connections[0], take_off_height, accuracy, init_time)
drone2_takeoff_thread = TakeoffThread(swarm_connections[1], take_off_height, accuracy, init_time)
drone3_takeoff_thread = TakeoffThread(swarm_connections[2], take_off_height, accuracy, init_time)

drone1_takeoff_thread.start()
drone2_takeoff_thread.start()
drone3_takeoff_thread.start()

drone1_takeoff_thread.join()
drone2_takeoff_thread.join()
drone3_takeoff_thread.join()

time.sleep(1)

print("all drones have taken off")


accuracy = .15

# swarm_target_positions = [[-1,.5,-.5],[0,.5,-.5],[1,.5,-.5]]
# goto_ned_threads = []

# for drone_connection, target_position in zip(swarm_connections, swarm_target_positions):
#     x = target_position[0]
#     y = target_position[1]
#     z = target_position[2]
#     goto_NED_point_thread = GotoNEDPointThread(drone_connection, x, y, z, init_time, accuracy)
#     goto_ned_threads.append(goto_NED_point_thread)

# for thread in goto_ned_threads:
#     thread.start()

# for thread in goto_ned_threads:
#     thread.join()

# swarm_target_positions = [[-1,-.5,-.5],[0,0,-.5],[1,-.5,-.5]]
# goto_ned_threads = []

# for drone_connection, target_position in zip(swarm_connections, swarm_target_positions):
#     x = target_position[0]
#     y = target_position[1]
#     z = target_position[2]
#     goto_NED_point_thread = GotoNEDPointThread(drone_connection, x, y, z, init_time, accuracy)
#     goto_ned_threads.append(goto_NED_point_thread)

# for thread in goto_ned_threads:
#     thread.start()

# for thread in goto_ned_threads:
#     thread.join()


# swarm_target_positions = [[-1,0,-.5],[0,0,-.5],[1,0,-.5]]
# goto_ned_threads = []

# for drone_connection, target_position in zip(swarm_connections, swarm_target_positions):
#     x = target_position[0]
#     y = target_position[1]
#     z = target_position[2]
#     goto_NED_point_thread = GotoNEDPointThread(drone_connection, x, y, z, init_time, accuracy)
#     goto_ned_threads.append(goto_NED_point_thread)

# for thread in goto_ned_threads:
#     thread.start()

# for thread in goto_ned_threads:
#     thread.join()

rotating_triangle = RotatingTriangle(25)

iterations = 20

accuracy = .20

while True:
    swarm_target_positions = rotating_triangle.get_triangle_coordinates()

    goto_ned_threads = []

    for drone_connection, target_position in zip(swarm_connections, swarm_target_positions):
        x = target_position[0]
        y = target_position[1]
        z = target_position[2]
        goto_NED_point_thread = GotoNEDPointThread(drone_connection, x, y, z, init_time, accuracy)
        goto_ned_threads.append(goto_NED_point_thread)

    for thread in goto_ned_threads:
        thread.start()

    for thread in goto_ned_threads:
        thread.join()
    iterations = iterations -1

    if iterations == 0:
        break


for drone in swarm_connections:
    set_mode_land(drone)

for drone in swarm_connections:
    disarm(drone)


time.sleep(2)

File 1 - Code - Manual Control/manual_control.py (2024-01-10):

from pickletools import float8
from pymavlink import mavutil
import math
import tkinter as tk
import pygame
import transformations as tft
from pyquaternion import Quaternion
import time

def get_distance_global(current_lat, current_lon, target_lat, target_lon):
    #return the distance between current position and target position in centimeters
    #does not account for the curvature of the earth

    delta_lat = target_lat - current_lat
    delta_lon = target_lon - current_lon

    if delta_lat <= 1 or delta_lon <= 1:
        return 0

    distance  = math.sqrt(delta_lat ** 2 + delta_lon ** 2) #formula for euclidean distance between 2 points
    return distance #mavlink GPS coords are represented in units of 10,000,000, so this line converts degrees to cm. 

def get_distance_local(curr_x, curr_y, curr_z, x, y, z):
    return math.sqrt((curr_x - x)**2 + (curr_y - y)**2 + (curr_z - z)**2)

def connect(port):
    print("Attempting to connect on port %d" % port)

    connection = mavutil.mavlink_connection('udpin:0.0.0.0:%d' % port) 

    connection.wait_heartbeat() #wait until we hear a heartbeat from the copter

    print("Connection success")
    print("Heartbeat from system (system %u component %u)" % (connection.target_system, connection.target_component))

    return connection 

def takeoff(connection, takeoff_alt):
    #set copter to guided mode
    connection.mav.set_mode_send(connection.target_system, mavutil.mavlink.MAV_MODE_FLAG_CUSTOM_MODE_ENABLED, 4) 

    #arm throttle
    connection.mav.command_long_send(connection.target_system, connection.target_component, 
                                 mavutil.mavlink.MAV_CMD_COMPONENT_ARM_DISARM, 0, 1, 0, 0, 0, 0, 0, 0)

    msg = connection.recv_match(type = 'COMMAND_ACK', blocking = True)
    print(msg) #"result: 0" if it executed without error. If you get result: 4, you probably need to set the copter to guided mode.

    #send takeoff command to target altitude.
    connection.mav.command_long_send(connection.target_system, connection.target_component, 
                                 mavutil.mavlink.MAV_CMD_NAV_TAKEOFF, 0, 0, 0, 0, 0, 0, 0, takeoff_alt)

    msg = connection.recv_match(type = 'COMMAND_ACK', blocking = True)
    print(msg)

    #loop until copter reaches takeoff altitude
    while 1:
        # Wait for the next LOCAL_POSITION_NED message
        msg = connection.recv_match(type='LOCAL_POSITION_NED', blocking=True)
    
        # Check if altitude is within a threshold of the target altitude
        if abs(msg.z * -1 - takeoff_alt) < 1.0:
            print("Reached target altitude")
            break

def land(connection): 
    connection.mav.command_long_send(connection.target_system, connection.target_component, 
                                mavutil.mavlink.MAV_CMD_NAV_LAND, 0, 0, 0, 0, 0, 0, 0, 0)

#send local frame coordinates and have copter fly over that spot.
def send_waypoint_local(connection, x, y, alt):
    connection.mav.send(mavutil.mavlink.MAVLink_set_position_target_local_ned_message
                    (10, connection.target_system, connection.target_component, mavutil.mavlink.MAV_FRAME_LOCAL_NED, 
                     int(0b010111111000), x, y, alt,
                      0, 0, 0, 0, 0, 0, 0, 0))

    while 1:
        msg = connection.recv_match(type = 'LOCAL_POSITION_NED', blocking = True)
        
        current_x = msg.x
        current_y = msg.y
        current_z = msg.z

        print("current x: %d" % current_x)

        distance = get_distance_local(current_x, current_y, current_z, x, y, alt)

        print("distance to target: %d" % distance)

        if(distance <= 3): #break when we are within 50 cm of target
            print("target waypoint reached")
            break


#send global gps coordinates and altitude, and have copter fly over that spot. 
def send_waypoint_global(connection, lat, lon, alt):
    connection.mav.send(mavutil.mavlink.MAVLink_set_position_target_global_int_message
                    (10, connection.target_system, connection.target_component, mavutil.mavlink.MAV_FRAME_GLOBAL_RELATIVE_ALT, 
                     int(0b110111111000), int(lat), int(lon), alt, 0, 0, 0, 0, 0, 0, 0, 0))
    #loop until we reach target waypoint
    while 1:
        msg = connection.recv_match(type = 'GLOBAL_POSITION_INT', blocking = True)

        current_lat = msg.lat 
        current_lon = msg.lon

        distance = get_distance_global(current_lat, current_lon, lat, lon)

        print("distance to target: %d" % distance)

        if(distance <= 50): #break when we are within 50 cm of target
            print("target waypoint reached")
            break

def euler_to_quaternion(roll, pitch, yaw):
    # Convert angles to radians
    roll = math.radians(roll)
    pitch = math.radians(pitch)
    yaw = math.radians(yaw)

    # Create a Quaternion from Euler angles
    quaternion = Quaternion(axis=[1, 0, 0], angle=roll) * Quaternion(axis=[0, 1, 0], angle=pitch) * Quaternion(axis=[0, 0, 1], angle=yaw)
    
    return quaternion

def send_manual_control(connection, x, y, z, r, buttons=0):
    """
    Send a MANUAL_CONTROL command to the drone.

    Parameters:
    - connection: The MAVLink connection object.
    - x: The x-axis value (pitch), normalized from -1000 to 1000.
    - y: The y-axis value (roll), normalized from -1000 to 1000.
    - z: The z-axis value (throttle), normalized from 0 to 1000.
    - r: The r-axis value (yaw), normalized from -1000 to 1000.
    - buttons: Bitmask of buttons pressed (default to 0).
    """

    # Ensure the values are within the acceptable range
    x = int(max(-1000, min(1000, x)))
    y = int(max(-1000, min(1000, y)))
    z = int(max(-1000, min(1000, z)))
    r = int(max(-1000, min(1000, r)))
    
    print(x,y,z,r)

    # Send the MANUAL_CONTROL message
    connection.mav.manual_control_send(
        connection.target_system,
        x,   # Pitch
        y,   # Roll
        z,   # Throttle
        r,   # Yaw
        buttons
    )
    
    duration = 10;

    #Hold the attitude for the specified duration
    if duration > 0:
        time.sleep(duration / 1000.0)
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

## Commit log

2024-01-08 Initial Commit
    Frame STLs, BOM, Manual control code, and the file structure. Motion capture code directory is still empty.
    [Bill Of Materials.xlsx, Drone Frame.3mf]
2024-01-10 updated manual_control with change mode, disarm, arm buttons and throttle throttling
2024-02-21 threaded code
2024-02-27 added more threads, added goto NED postion funciton
2024-03-27 created threaded landing and goto ned threads for swarm
2024-04-10 threading updates
